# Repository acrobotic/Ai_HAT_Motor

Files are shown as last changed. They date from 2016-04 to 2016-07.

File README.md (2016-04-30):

## Ai\_HAT\_Motor

PCB design files (EAGLE) for a Raspberry Pi A+/B+/2/3 HAT carrying a motor
and servo driver ICs (DRV8835 and PCA9685, respectively), as well as a 4-Channel 
ADC (ADS1115). 

## Description

Visit our online shop at:

   * https://acrobotic.com/

Designed by ACROBOTIC Industries.  Please consider buying products from us to 
help fund future Open-Source projects like this! We’ll always put our best 
effort in every project, and release all our design files and code for you to 
use. 

## License

Released under the Creative Commons Attribution, Share-Alike license. Please 
check LICENSE.txt for more information. All text above must be included in any 
redistribution.

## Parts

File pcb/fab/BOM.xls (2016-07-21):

Ai HAT Motor – BOM
Cisco Zabala (x1sc0@acrobotic.com) last updated: 21.07.2016
Vendor | Vendor Part Number | SKU | Type | Designator | Qty | Description | Case | SMD, BGA, LCC, OR TH | Notes
Digi-Key | 311-3.9KGRTR-ND | RES-00003-239 | Resistors | R1, R2 | 2 | RES 3.9K OHM 1/10W SMD 0603 | 0603 | SMD | DNI
Digi-Key | 311-1.0KGRTR-ND | RES-00003-210 |  | R3 | 1 | RES 1K OHM 1/10W SMD 0603 | 0603 | SMD | DNI
Digi-Key | 311-10KGRTR-ND | RES-00003-310 |  | R4, R5, R6, R7, R8, R9, R14 | 7 | RES 10K OHM 1/10W SMD 0603 | 0603 | SMD
Digi-Key | 311-220GRTR-ND | RES-00003-310 |  | R10, R11, R12, R13 | 4 | RES 220 OHM 1/10W SMD 0603 | 0603 | SMD
Digi-Key | 490-5881-2-ND | CAP-00004-410 | Capacitors | C1, C4, C6 | 3 | CAP CER 0.1UF 10V 5% 0603 | 0603 | SMD
Digi-Key | 490-3297-2-ND | CAP-00004-547 | LEDs | C2 | 1 | CAP CER 4.7UF 10V 5% 0603 | 0603 | SMD
Digi-Key | 490-3298-2-ND | CAP-00004-610 |  | C3, C5, C7 | 3 | CAP CER 10UF 10V 5% 0603 | 0603 | SMD
Digi-Key | 24LC32AT-I/OTTR-ND | CHP-00036 | ICs | EEPROM | 1 | IC EEPROM 32KBIT 400KHZ 8SOIC (24LC32A) |  | SMD | DNI
Digi-Key | 296-30391-2-ND | CHP-00059 |  | U1 | 1 | DUAL LOW-VOLTAGE H-BRIDGE (DRV8835) |  | SMD
Digi-Key | 296-24934-1-ND | CHP-00054 |  | U2 | 1 | IC ADC 16-BIT I2C PROGBL 10-MSOP (ADS1115) |  | SMD
Digi-Key | 568-11925-1-ND | CHP-00013 |  | IC1 | 1 | IC PWM CTLR LED DVR 28TSSOP (PCA9685) |  | SMD
Digi-Key | 785-1106-1-ND | CHP-00052 |  | Q1 | 1 | SMD MOSFET P-CHANNEL 30V 25A TO252 (AOD417) |  | SMD
Digi-Key | 609-4618-1-ND | CON-00014 | Connectors | PWR_IN | 1 | CONN USB MICRO B RECPT SMT R/A |  | TH
Digi-Key | ED2635-ND | CON-00007 |  | MOTA, MOTB | 2 | 2-Pin Screw Terminal Block (3.5mm) |  | TH | DNI
 |  | CON-00031 |  | 5V, GND, 3V3, ULTRASONIC, ANALOG, PI_PWR, MOTA_ENCA, MOTB_ENCB, J1, J2, J3, J4 | 2 | Break-away Pin Connector, 0.1in Pitch, 1×40 (Male, Double, TH) |  | TH | DNI
 |  | CON-00042 |  | K1 | 2 | Pin Connector, 0.1in Pitch, 2x20, Tall (Female, TH) |  | TH | DNI

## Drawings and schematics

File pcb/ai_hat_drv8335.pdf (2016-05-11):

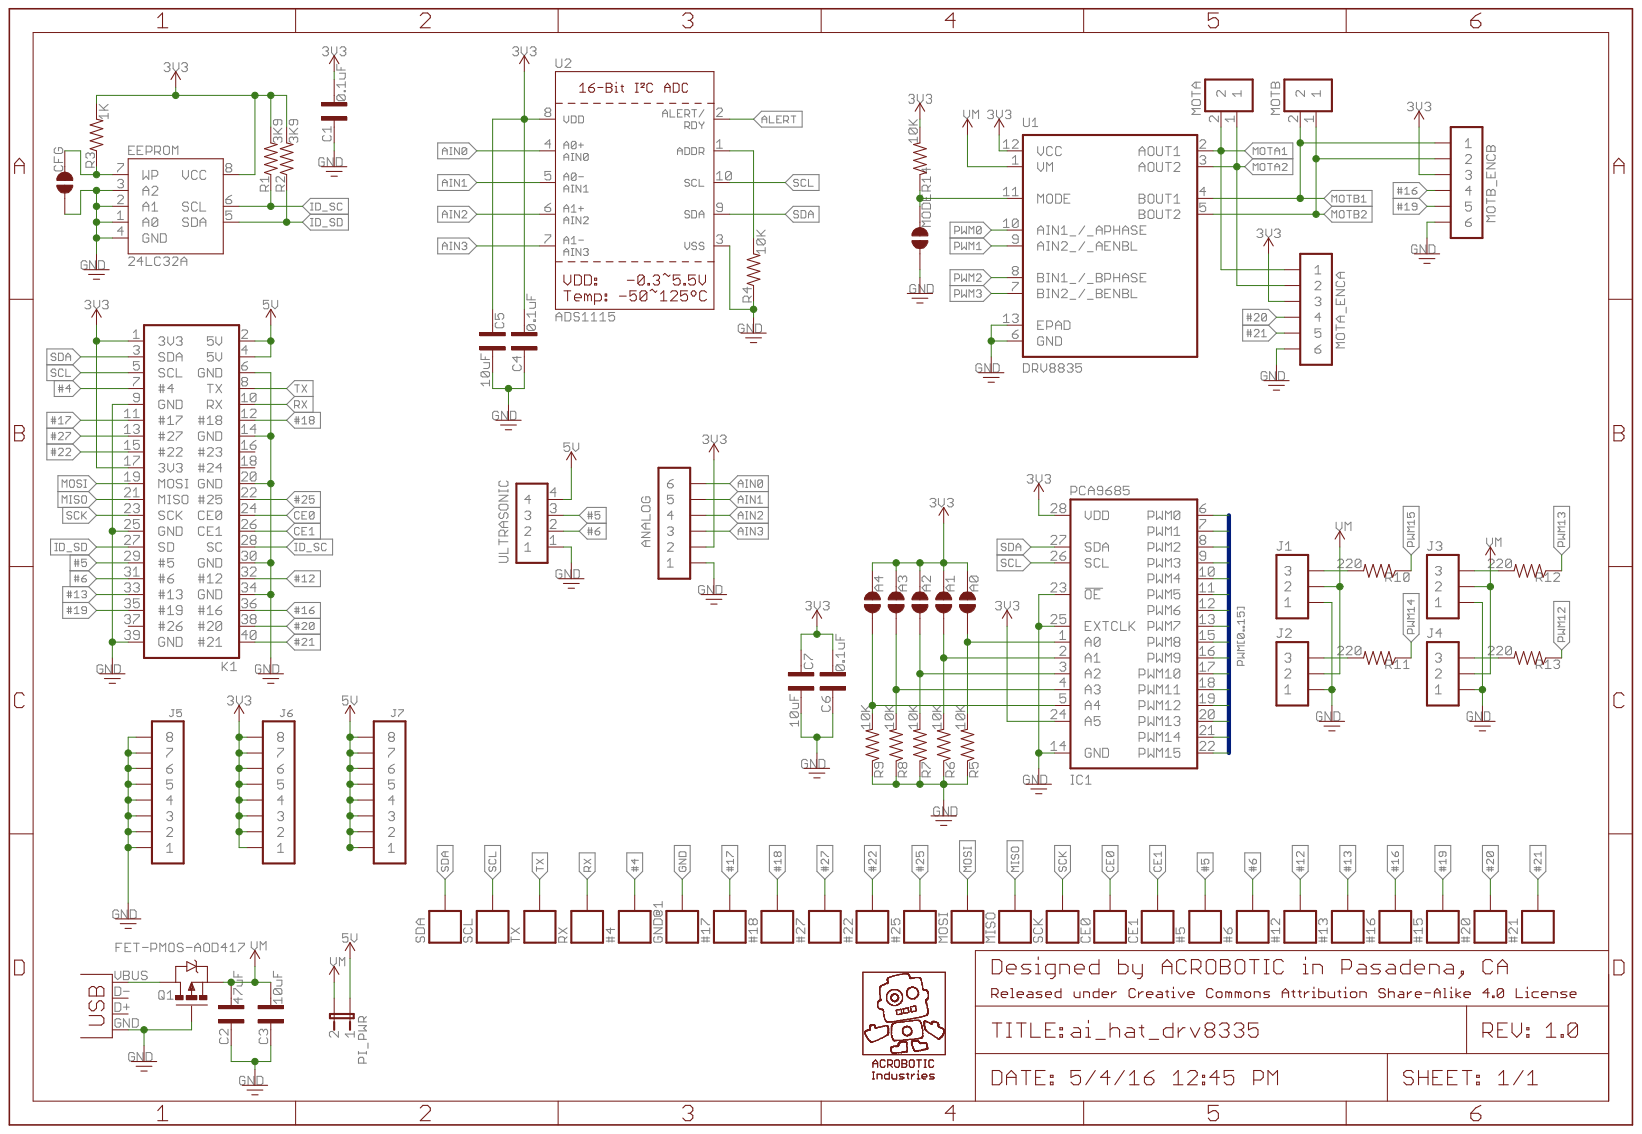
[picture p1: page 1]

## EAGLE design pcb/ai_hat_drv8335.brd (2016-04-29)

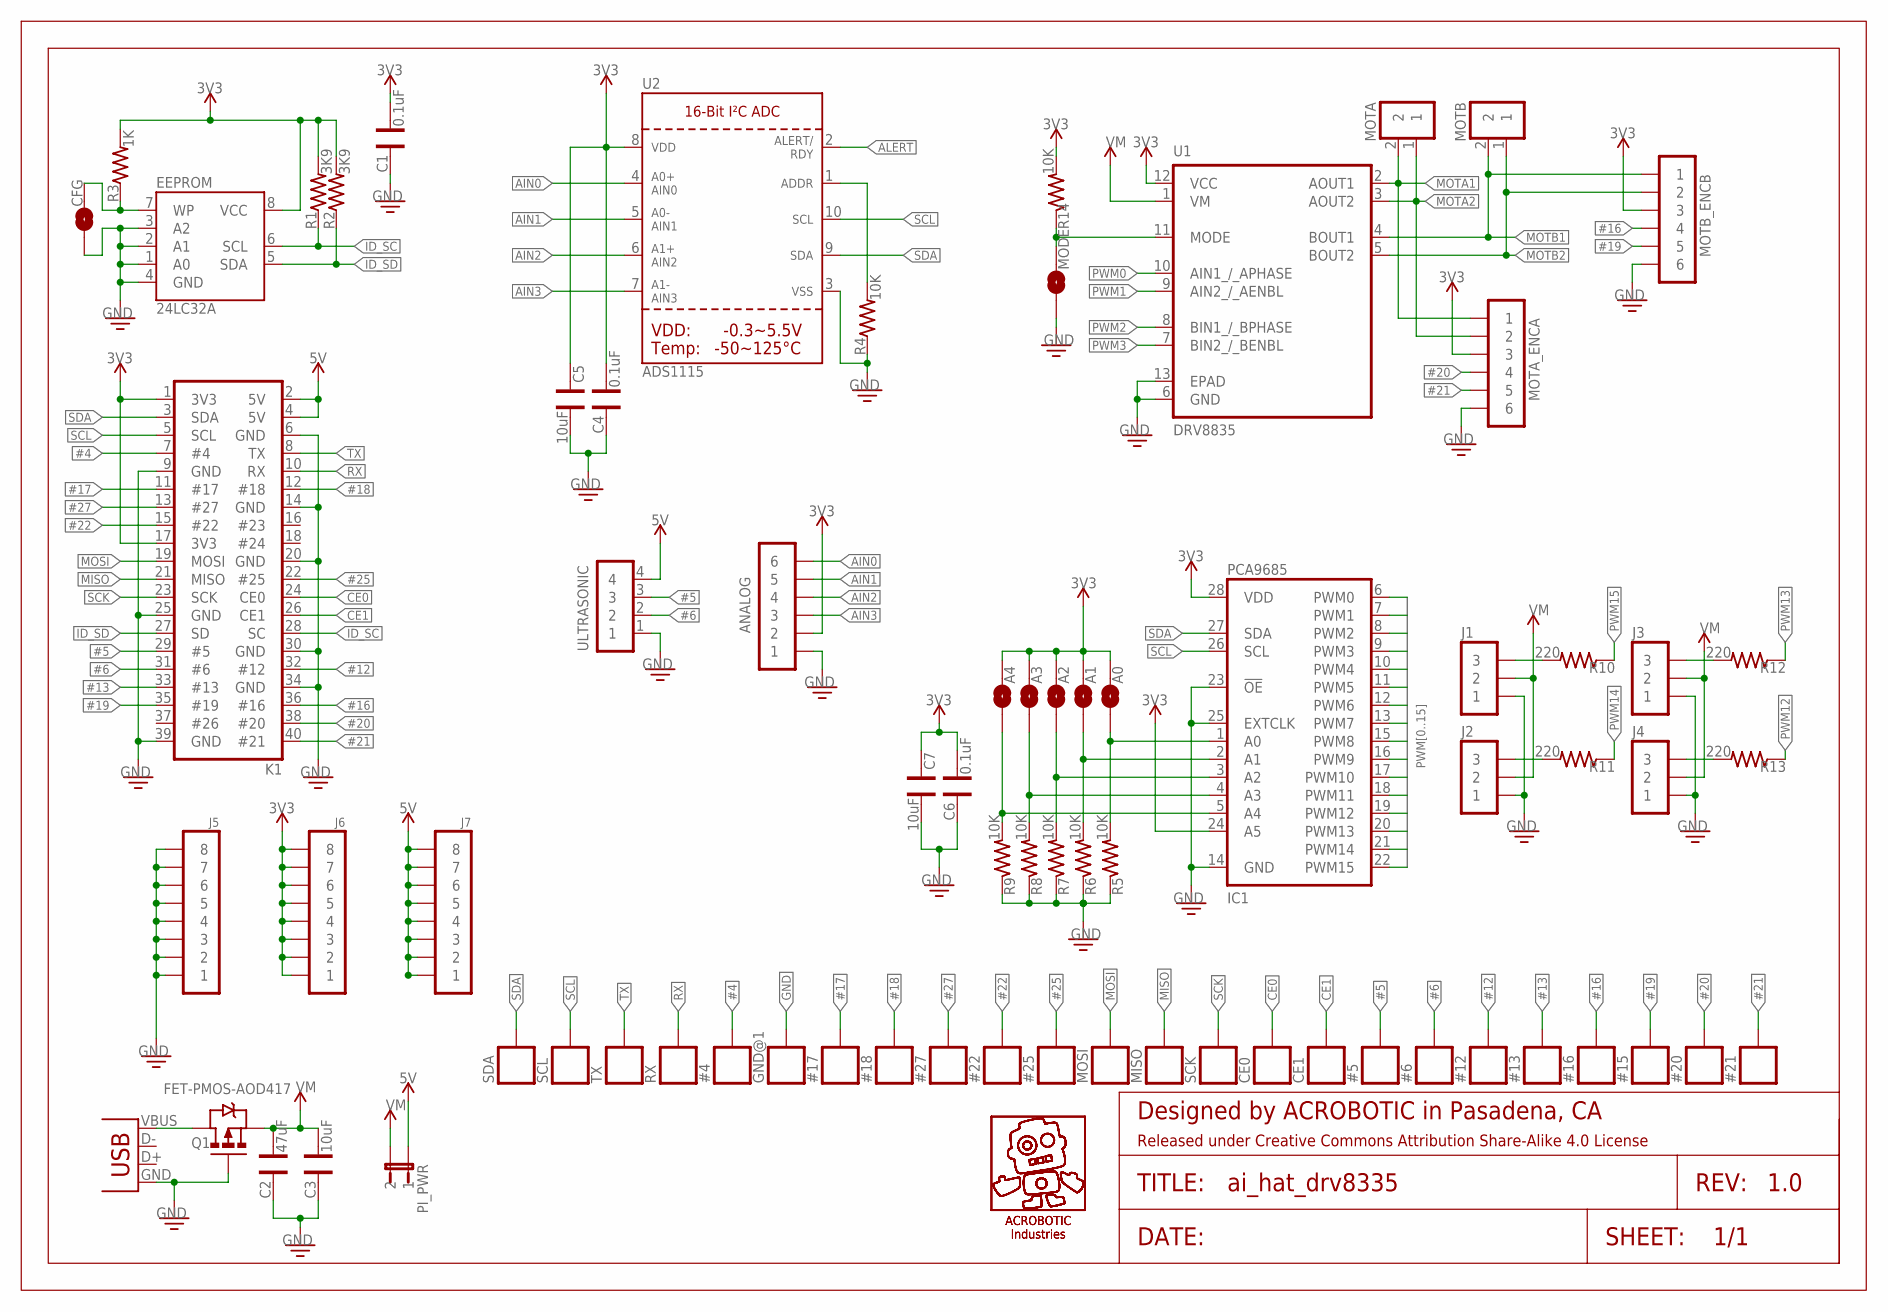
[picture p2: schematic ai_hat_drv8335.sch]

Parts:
#4, #5, #6, #12, #13, #15, #16, #17, #18, #20, #21, #22, #25, #27: 1X01-SM
A0, A1, A2, A3, A4: 1X02-SJ-NO
ANALOG: 1X06
C1: 0.1uF; CAP-0603
C2: 47uF; CAP-0603
C3: 10uF; CAP-0603
C4, C6: 0.1uF; CAP-0402
C5, C7: 10uF; CAP-0402
CE0, CE1: 1X01-SM
CFG: 1X02-SJ-NO
EEPROM: 24LC32A; SO08-EIAJ
FRAME1: FRAME-LETTER; CREATIVE-COMMONS
GND@1: 1X01-SM
IC1: PCA9685; TSSOP28
J1, J2, J3, J4: 1X03
J5, J6, J7: 1X08
K1: 2X20-RPI-ALT
MISO: 1X01-SM
MODE: 1X02-SJ-NO
MOSI: 1X01-SM
MOTA: 1X02ST; 1X02-ST
MOTA_ENCA: 1X06
MOTB: 1X02ST; 1X02-ST
MOTB_ENCB: 1X06
PI_PWR: 1X02-PJ; 1X02
PWR_IN: USBMICROB-PTH; USB-MICROB-TH
Q1: FET-PMOS-AOD417; TO-252
R1, R2: 3K9; RES-0603; TOLERANCE 5%
R3: 1K; RES-0603; TOLERANCE 5%
R4: 10K; RES-0402
R5, R6, R7, R8, R9, R14: 10K; RES-0603; TOLERANCE 5%
R10, R11, R12, R13: 220; RES-0603; TOLERANCE 5%
RX: 1X01-SM
SCK: 1X01-SM
SCL: 1X01-SM
SDA: 1X01-SM
TX: 1X01-SM
U1: DRV8835; 12SON
U2: ADS1115; MSOP10
U$9, U$10: AI-LOGOXS; AI-LOGO-XS
ULTRASONIC: 1X04

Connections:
3V3: A0.2, A1.2, A2.2, A3.2, A4.2, ANALOG.2, C1.1, C4.1, C5.2, C6.1, C7.2, EEPROM.8 (VCC), IC1.24 (A5), IC1.28 (VDD), J6.1, J6.2, J6.3, J6.4, J6.5, J6.6, J6.7, J6.8, K1.1 (3V3), K1.17 (3V3), MOTA_ENCA.3, MOTB_ENCB.3, R1.2, R2.2, R3.2, R14.2, U1.12 (VCC), U2.8 (VDD)
5V: J7.1, J7.2, J7.3, J7.4, J7.5, J7.6, J7.7, J7.8, K1.2 (5V), K1.4 (5V), PI_PWR.1, ULTRASONIC.4
#4: #4.1, K1.7 (#4)
#5: #5.1, K1.29 (#5), ULTRASONIC.3
#6: #6.1, K1.31 (#6), ULTRASONIC.2
#12: #12.1, K1.32 (#12)
#13: #13.1, K1.33 (#13)
#16: #16.1, K1.36 (#16), MOTB_ENCB.4
#17: #17.1, K1.11 (#17)
#18: #18.1, K1.12 (#18)
#19: #15.1, K1.35 (#19), MOTB_ENCB.5
#20: #20.1, K1.38 (#20), MOTA_ENCA.4
#21: #21.1, K1.40 (#21), MOTA_ENCA.5
#22: #22.1, K1.15 (#22)
#25: #25.1, K1.22 (#25)
#27: #27.1, K1.13 (#27)
A0: A0.1, IC1.1 (A0), R5.2
A1: A1.1, IC1.2 (A1), R6.2
A2: A2.1, IC1.3 (A2), R7.2
A3: A3.1, IC1.4 (A3), R8.2
A4: A4.1, IC1.5 (A4), R9.2
AIN0: ANALOG.6, U2.4 (AIN0)
AIN1: ANALOG.5, U2.5 (AIN1)
AIN2: ANALOG.4, U2.6 (AIN2)
AIN3: ANALOG.3, U2.7 (AIN3)
ALERT: U2.2 (ALERT/RDY)
CE0: CE0.1, K1.24 (CE0)
CE1: CE1.1, K1.26 (CE1)
GND: ANALOG.1, C1.2, C2.2, C3.2, C4.2, C5.1, C6.2, C7.1, CFG.1, EEPROM.1 (A0), EEPROM.2 (A1), EEPROM.3 (A2), EEPROM.4 (GND), GND@1.1, IC1.14 (GND), IC1.23 (!OE), IC1.25 (EXTCLK), J1.1, J2.1, J3.1, J4.1, J5.1, J5.2, J5.3, J5.4, J5.5, J5.6, J5.7, J5.8, K1.6 (GND), K1.9 (GND), K1.14 (GND), K1.20 (GND), K1.25 (GND), K1.30 (GND), K1.34 (GND), K1.39 (GND), MODE.1, MOTA_ENCA.6, MOTB_ENCB.6, PWR_IN.GND, Q1.G, R4.1, R5.1, R6.1, R7.1, R8.1, R9.1, U1.6 (GND), U1.13 (EPAD), U2.3 (VSS), ULTRASONIC.1
ID_SC: EEPROM.6 (SCL), K1.28 (SC), R1.1
ID_SD: EEPROM.5 (SDA), K1.27 (SD), R2.1
MISO: K1.21 (MISO), MISO.1
MOSI: K1.19 (MOSI), MOSI.1
MOTA1: MOTA.2, MOTA_ENCA.1, U1.2 (AOUT1)
MOTA2: MOTA.1, MOTA_ENCA.2, U1.3 (AOUT2)
MOTB1: MOTB.2, MOTB_ENCB.1, U1.4 (BOUT1)
MOTB2: MOTB.1, MOTB_ENCB.2, U1.5 (BOUT2)
unnamed: R4.2, U2.1 (ADDR)
unnamed: MODE.2, R14.1, U1.11 (MODE)
unnamed: CFG.2, EEPROM.7 (WP), R3.1
unnamed: PWR_IN.VBUS, Q1.D
unnamed: J1.3, R10.2
unnamed: J4.3, R13.2
unnamed: J3.3, R12.2
unnamed: J2.3, R11.2
PWM0: IC1.6 (PWM0), U1.10 (AIN1_/_APHASE)
PWM1: IC1.7 (PWM1), U1.9 (AIN2_/_AENBL)
PWM2: IC1.8 (PWM2), U1.8 (BIN1_/_BPHASE)
PWM3: IC1.9 (PWM3), U1.7 (BIN2_/_BENBL)
PWM4: IC1.10 (PWM4)
PWM5: IC1.11 (PWM5)
PWM6: IC1.12 (PWM6)
PWM7: IC1.13 (PWM7)
PWM8: IC1.15 (PWM8)
PWM9: IC1.16 (PWM9)
PWM10: IC1.17 (PWM10)
PWM11: IC1.18 (PWM11)
PWM12: IC1.19 (PWM12), R13.1
PWM13: IC1.20 (PWM13), R12.1
PWM14: IC1.21 (PWM14), R11.1
PWM15: IC1.22 (PWM15), R10.1
RX: K1.10 (RX), RX.1
SCK: K1.23 (SCK), SCK.1
SCL: IC1.26 (SCL), K1.5 (SCL), SCL.1, U2.10 (SCL)
SDA: IC1.27 (SDA), K1.3 (SDA), SDA.1, U2.9 (SDA)
TX: K1.8 (TX), TX.1
VM: C2.1, C3.1, J1.2, J2.2, J3.2, J4.2, PI_PWR.2, Q1.S, U1.1 (VM)

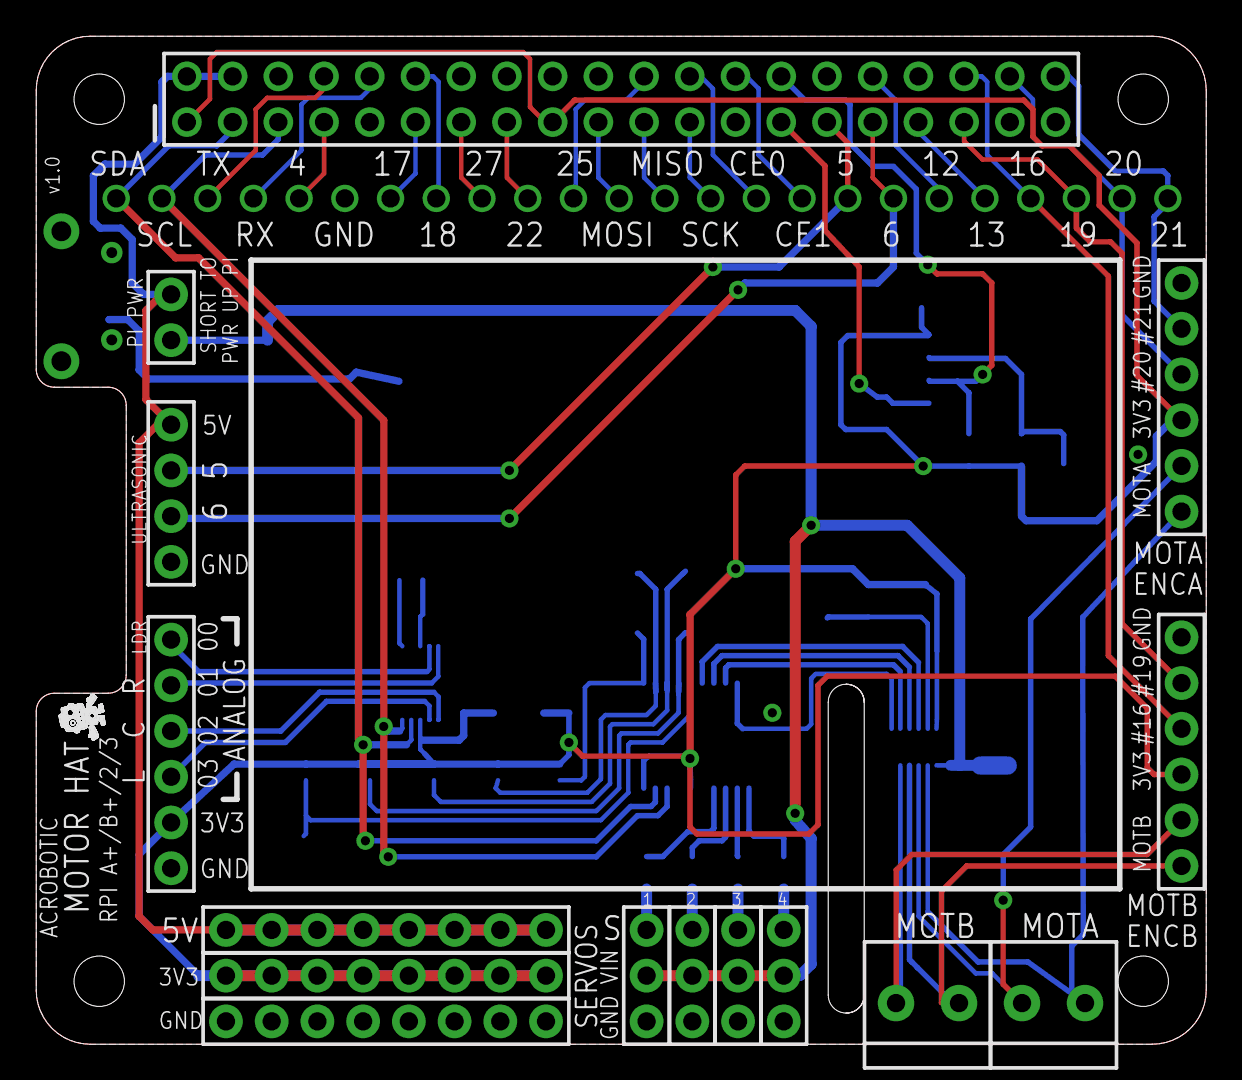
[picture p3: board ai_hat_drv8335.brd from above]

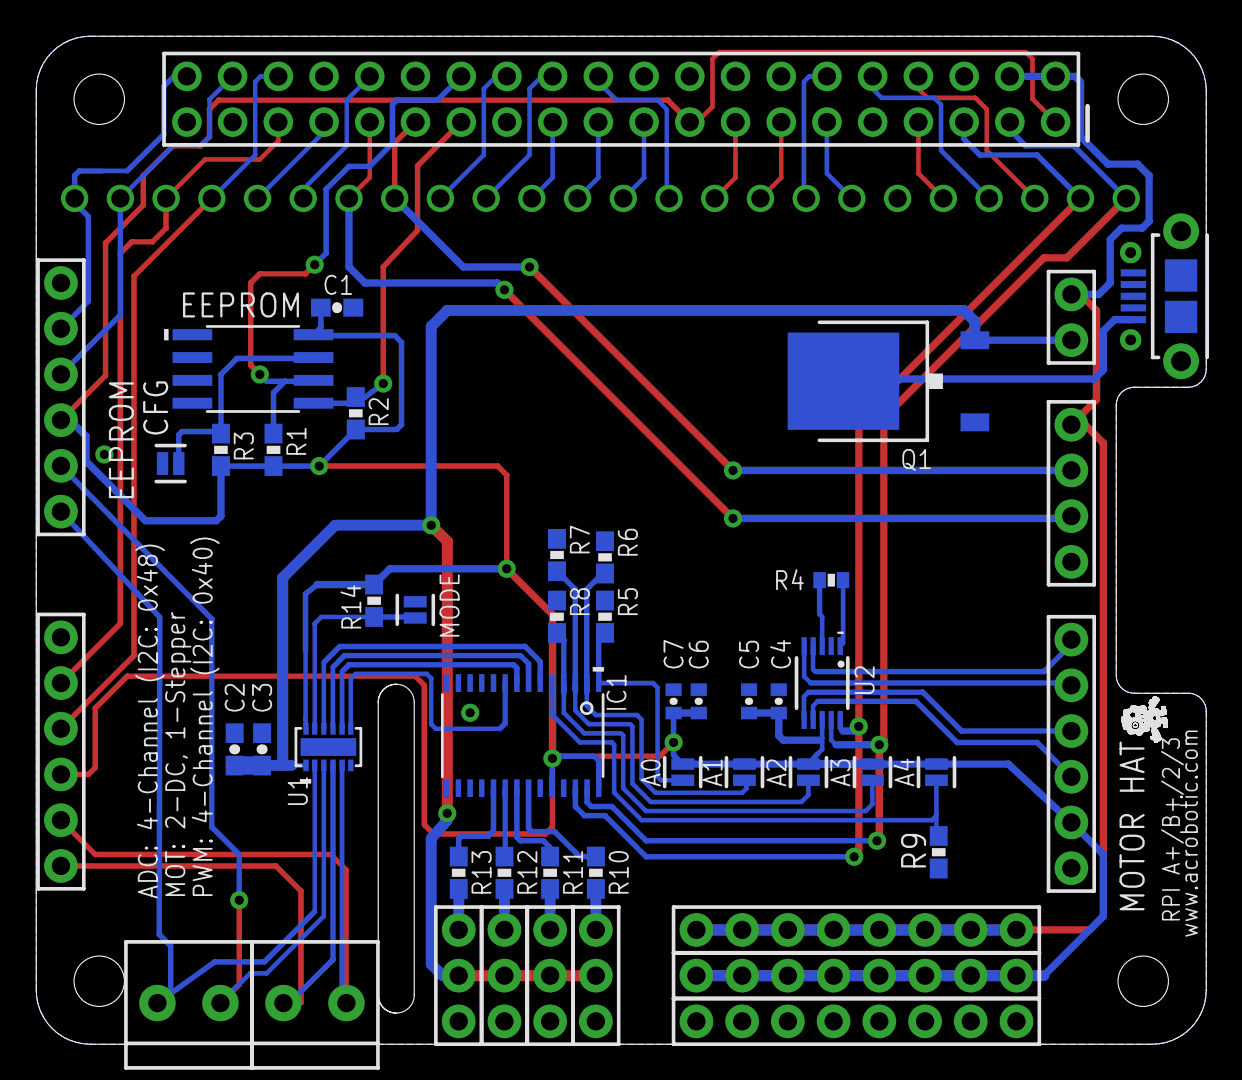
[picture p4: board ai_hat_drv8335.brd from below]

Board: 2 copper layers, 65.0 x 56.0 mm, 76 parts (35 on the bottom side), 58 nets.

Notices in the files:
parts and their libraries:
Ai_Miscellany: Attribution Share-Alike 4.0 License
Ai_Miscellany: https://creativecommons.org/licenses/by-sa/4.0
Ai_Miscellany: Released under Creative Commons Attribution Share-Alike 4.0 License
